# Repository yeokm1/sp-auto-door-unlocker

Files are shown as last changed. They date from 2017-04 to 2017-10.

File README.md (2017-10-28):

# Auto Door Unlocker

A device at the exit that unlocks the main office door of the Singapore Power Digital Team's office at Keppel Tower 2 with just a hand gesture. There are several iterations

1. Passive Infrared (PIR) sensor
2. Active IR sensor
3. Active IR and Ultrasonic sensor

## Demo media

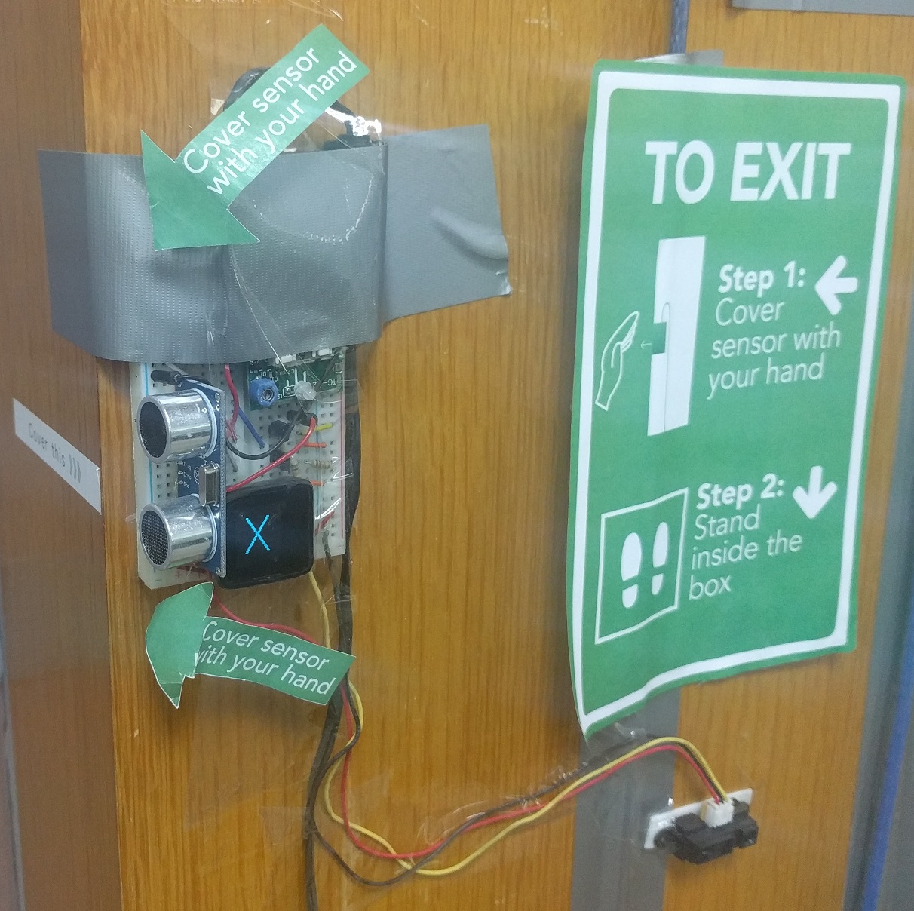
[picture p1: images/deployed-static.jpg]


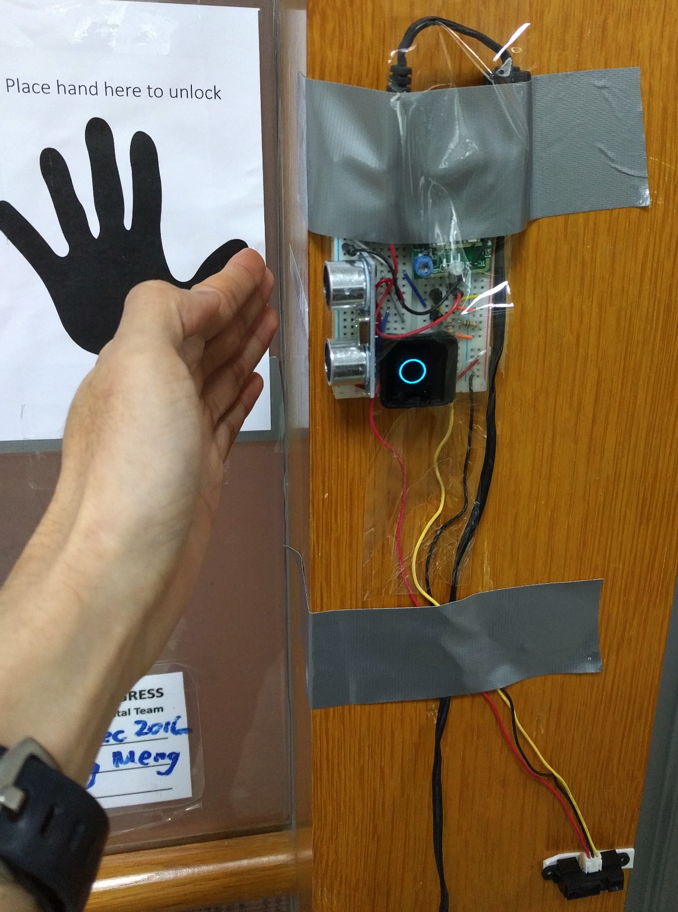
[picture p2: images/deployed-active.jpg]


(https://www.youtube.com/watch?v=IeWPlm1Xaz0)

## How it works?

This device leverages on the original wireless remote to do the unlocking as seen in the picture below.

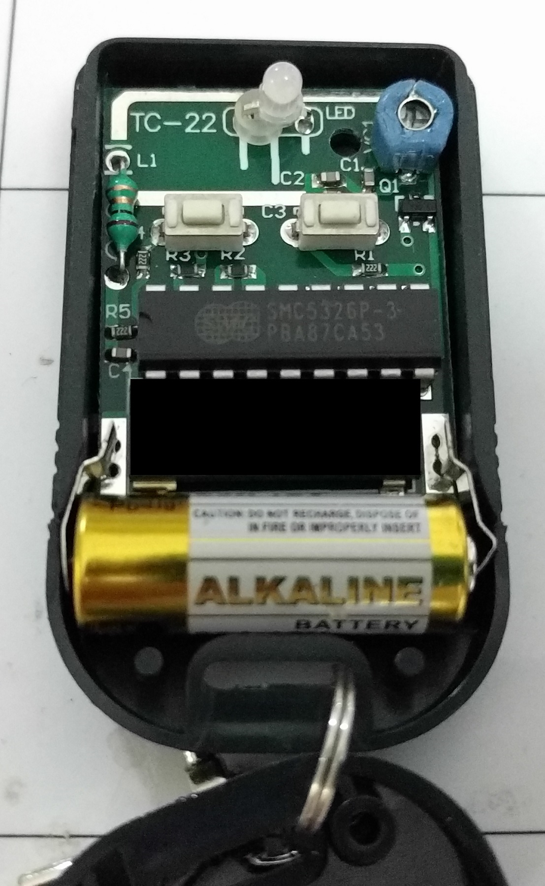
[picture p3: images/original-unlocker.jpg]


To detect the hand gesture, an active Infrared Sensor is used to detect changes in the environment infrared signature.

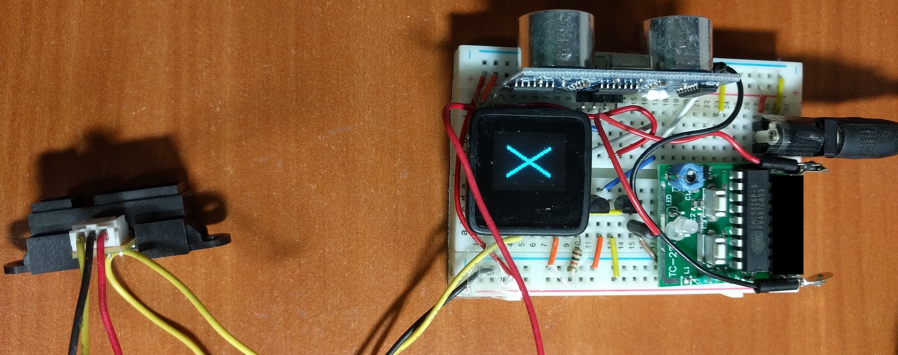
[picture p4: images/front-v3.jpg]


The IR sensor sends an analog signal to the Microview microcontroller indicating the distance of the object in front of it. If the threshold is hit, the Microview then simulates a button press by applying a voltage on the button circuit on the remote to send the wireless signal to unlock the doors. An animation is also shown on the OLED screen of the Microview.

A 2 seconds delay is imposed on the initial power on of the device to let the sensors "settle" down

## Schematic

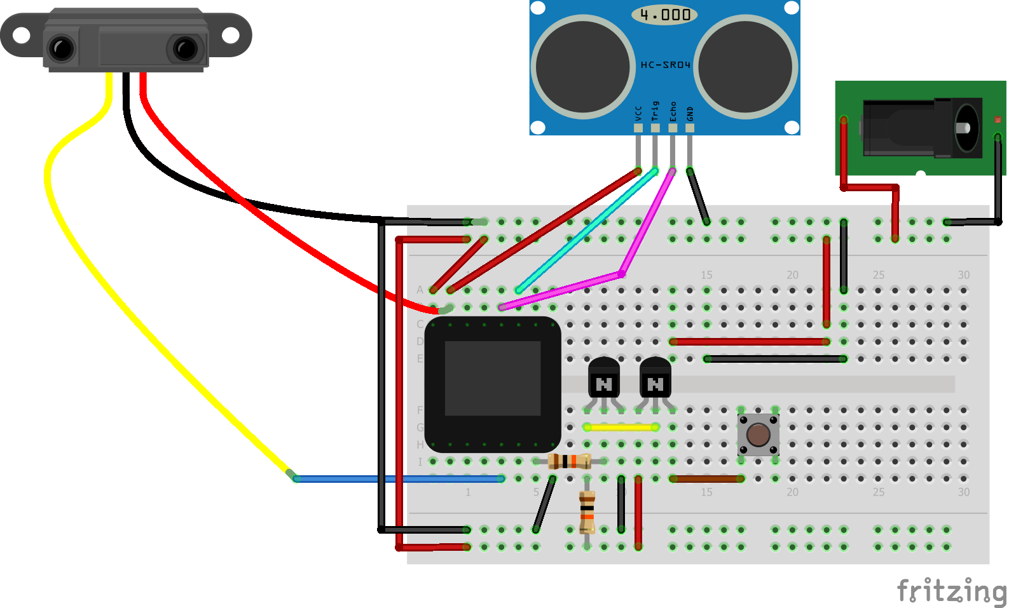
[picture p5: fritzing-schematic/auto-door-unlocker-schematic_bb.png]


A Fritzing drawing indicates the connections on the breadboard. Note this is just a guide of connection and not representative of the actual physical layout.

The button circuit on the remote requires a 12V input to engage. I had to use 2 transistors to switch the input as the output pin on both the Microview do not seem to be able to saturate the transistor. Engaging the button requires an opposite signal, output LOW to "press" the button and vice-versa.

## Parts required
1. MV1: [Microview module](https://www.sparkfun.com/products/12923)
2. J3: [Sharp GP2Y0A21YK IR sensor 10-80cm](http://www.sgbotic.com/index.php?dispatch=products.view&product_id=20)
3. hc-sr1: [HC-SR04 v2](http://www.sgbotic.com/index.php?dispatch=products.view&product_id=1855)
3. R1 and R2: 10K ohm resistors
4. U1 and U2: [P2N2222A NPN transistor](http://www.sgbotic.com/index.php?dispatch=products.view&product_id=773)
5. J2: [2.1mm DC barrel jack](https://www.adafruit.com/product/373)

## Setting up the IDE for compilation

1. Programming the Microview requires one-time use of the [Microview USB Programmer](https://www.sparkfun.com/products/12924)
2. You can follow the Arduino set up guide in this [link](http://microview.io/intro/getting-started.html) which is summarised in the subsequent steps I recommend the native Arduino IDE instead of Codebender.
3. Download the latest [Arduino IDE](https://www.arduino.cc/en/Main/Software) which is version 1.6.13 at time of writing.
4. `git clone https://github.com/geekammo/MicroView-Arduino-Library.git` to your Arduino library folder which is `~/Documents/Arduino/libraries` directory on Macs.
5. Open the `auto-door-unlocker-code` file with the Arduino IDE and select Arduino/Genuino Uno as the board type. Make sure to choose the correct serial port associated with the USB programmer.
6. Just hit upload button to program the board.

## References and libraries

1. [Control 12V from 5V signal](https://electronics.stackexchange.com/a/70246)
2. [Hand image](https://pixabay.com/p-297767/)
3. [Sharp IR library](https://github.com/guillaume-rico/SharpIR)
4. [Ultrasonic HC-SR04](http://randomnerdtutorials.com/complete-guide-for-ultrasonic-sensor-hc-sr04/)

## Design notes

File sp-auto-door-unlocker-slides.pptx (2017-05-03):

## SP Office Gadget: Auto Door Unlocker

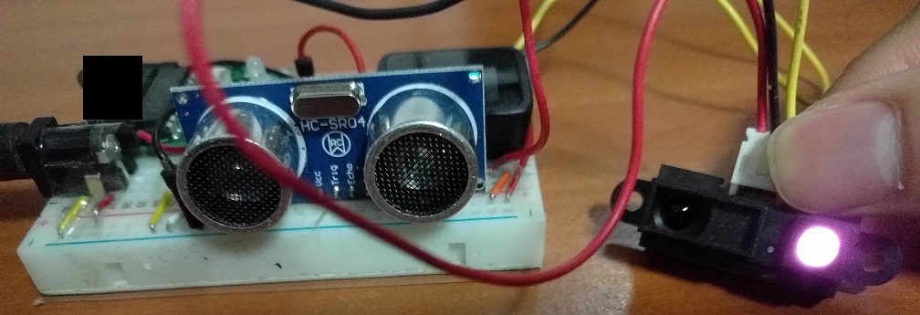
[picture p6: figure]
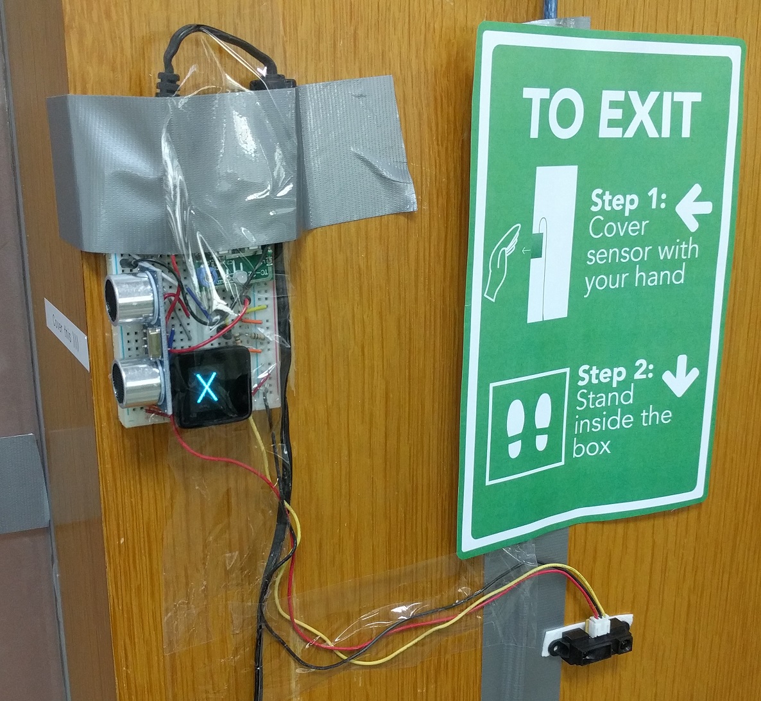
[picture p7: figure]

By: Yeo Kheng Meng (yeokm1@gmail.com)
https://github.com/yeokm1/sp-auto-door-unlocker


Hackware v3.0 (3 May 2017)
SP Digital Tech Talk (29 Dec 2016)

## Problem?

- Tap staff pass on exit
  - Trouble for visitors
  - Hassle of taking out pass
- Solution:
  - Exit without tapping pass

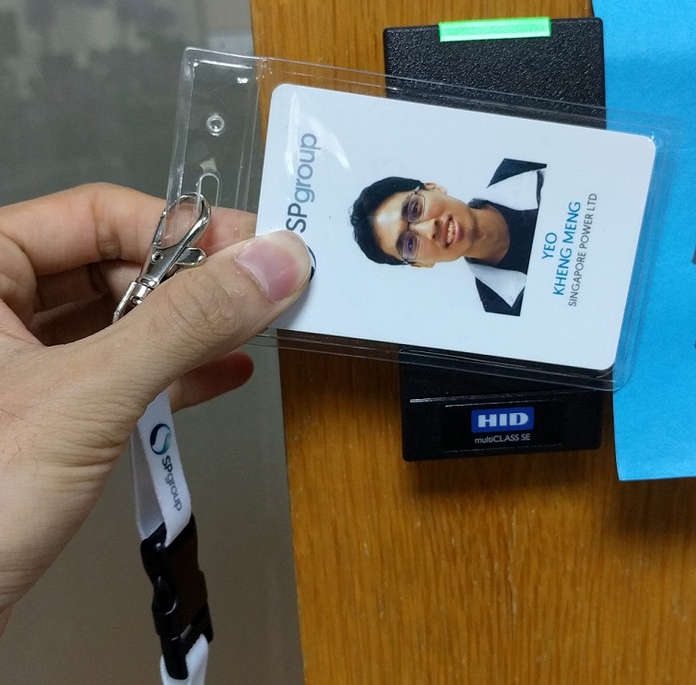
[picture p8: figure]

## Demo Video

https://www.youtube.com/watch?v=IeWPlm1Xaz0

## Wireless remote unlocker

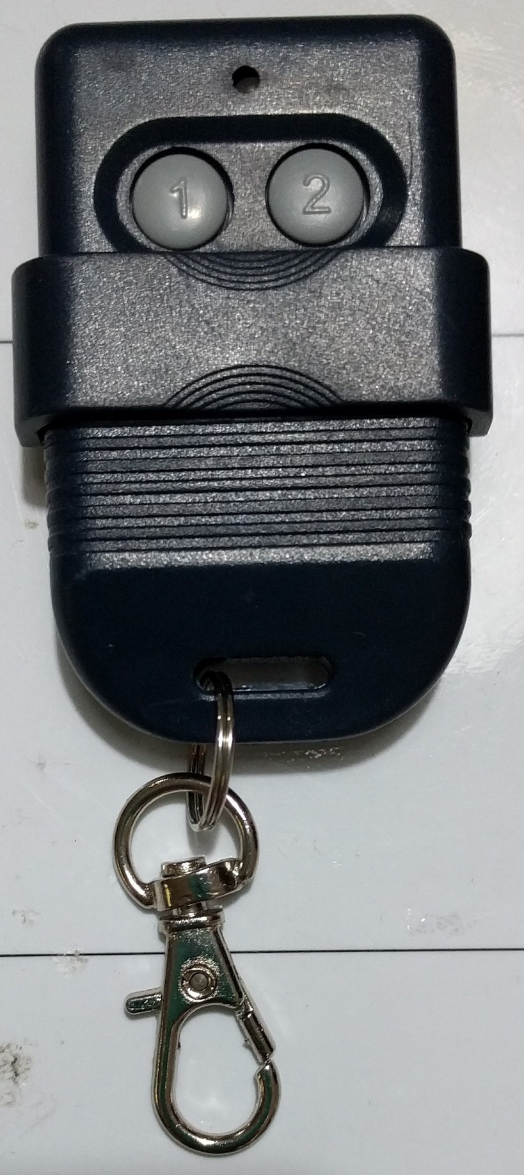
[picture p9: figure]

- 12V battery source
- 2 buttons
- DIP code-select switch
- Voltage-controlled oscillator (VCO)
  - Frequency determined by voltage
- 330Mhz SMC5326P-3
  - Some China chip
  - Unknown function
  - Cannot locate data sheet

## How the button triggers the signal?

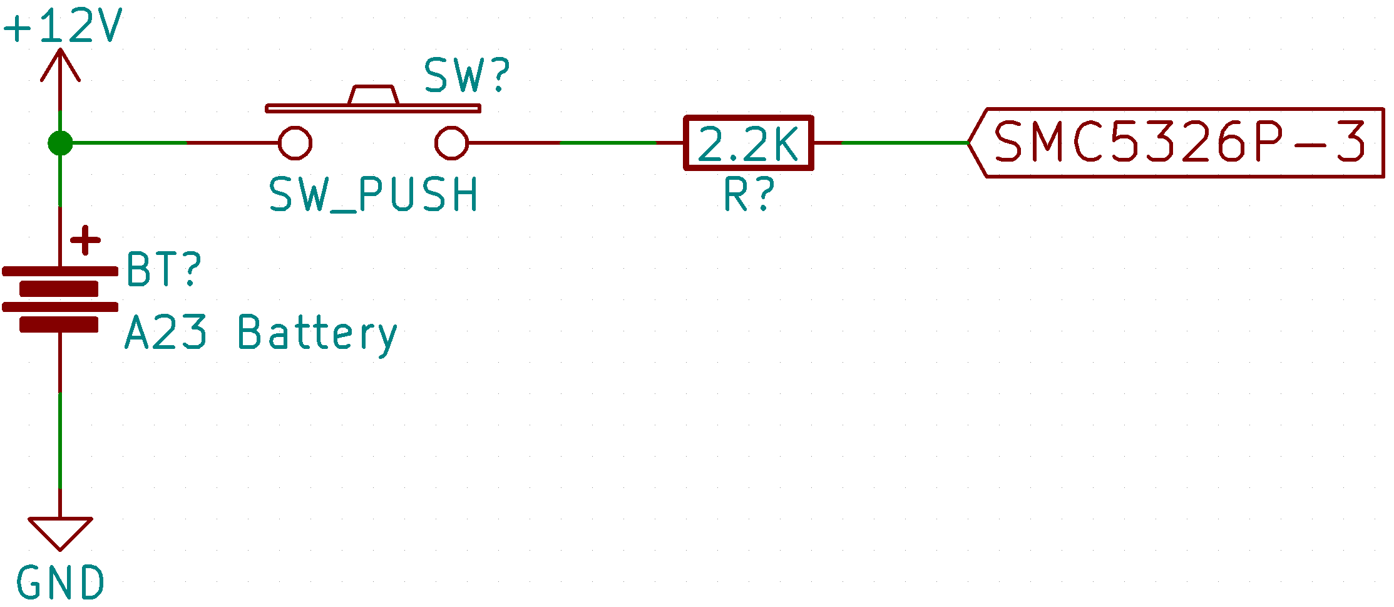
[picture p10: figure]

## An electronic switch: Transistor

- Control current flow with another current flow

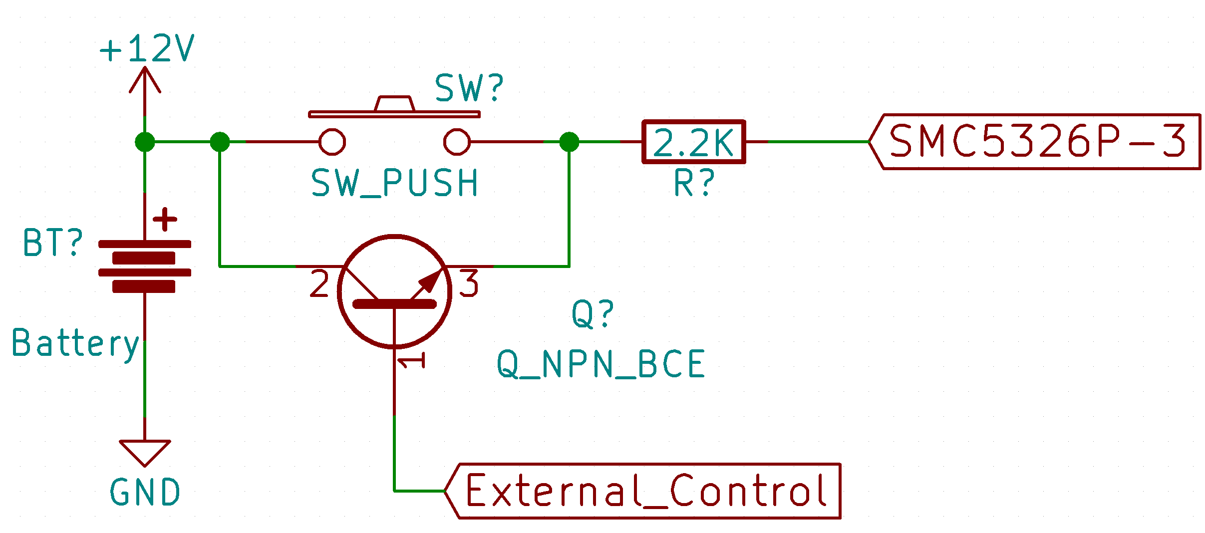
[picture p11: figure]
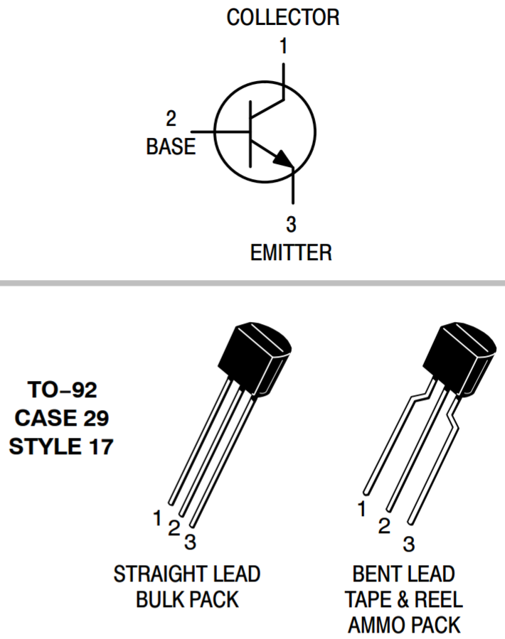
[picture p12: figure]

## The trigger: Active IR + Ultrasonic Sensor

- Ultrasonic HC-SR04 v2
  - 3.3V logic compatible
  - Physical Domain
- Infrared (IR) Distance Sensor GP2Y0A21YKR
  - Effective range: 10 to 80cm
  - Active IR
  - Electromagnetic domain
- => Multi-modal integration / Sensor Fusion to avoid errors

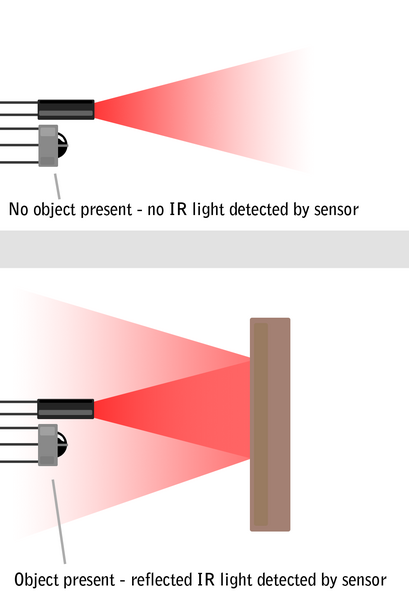
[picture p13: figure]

Source: http://education.rec.ri.cmu.edu/content/electronics/boe/ir_sensor/1.html

## The brain: Microview

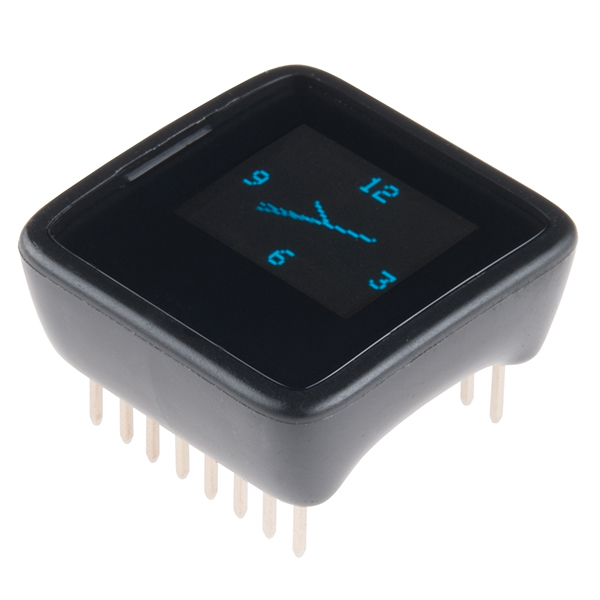
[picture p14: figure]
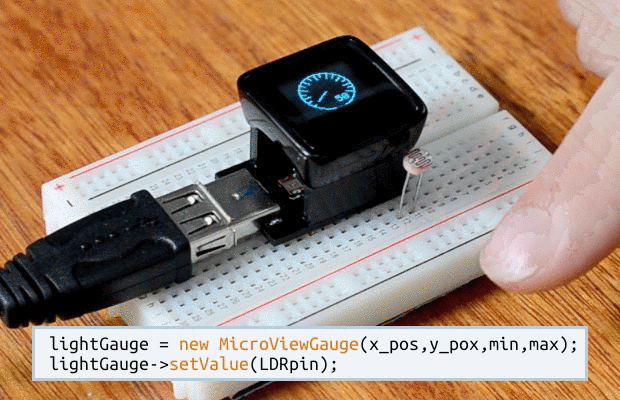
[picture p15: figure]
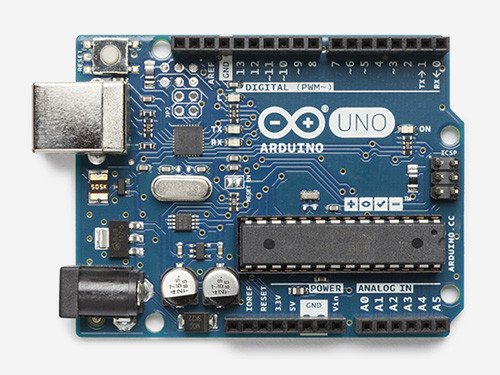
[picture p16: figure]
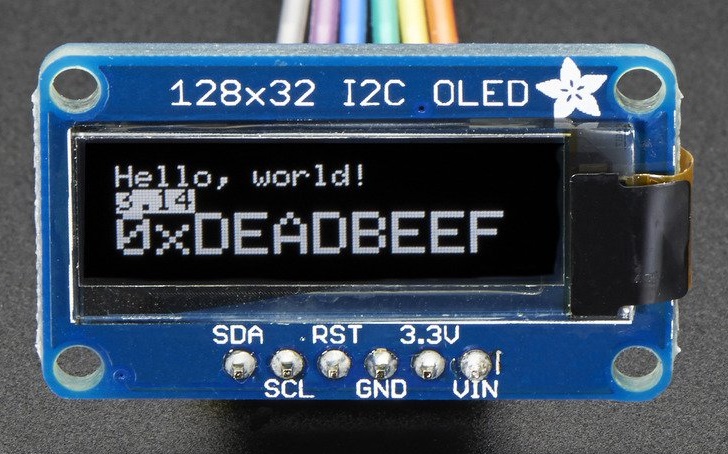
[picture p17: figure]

=

+

- Microview = Arduino + 64x48 OLED screen
- Runs on ATmega328P chip as with Arduino Uno

Source: http://makezine.com/2014/03/25/interview-with-marcus-schappi/

## Wireless Remote Modification

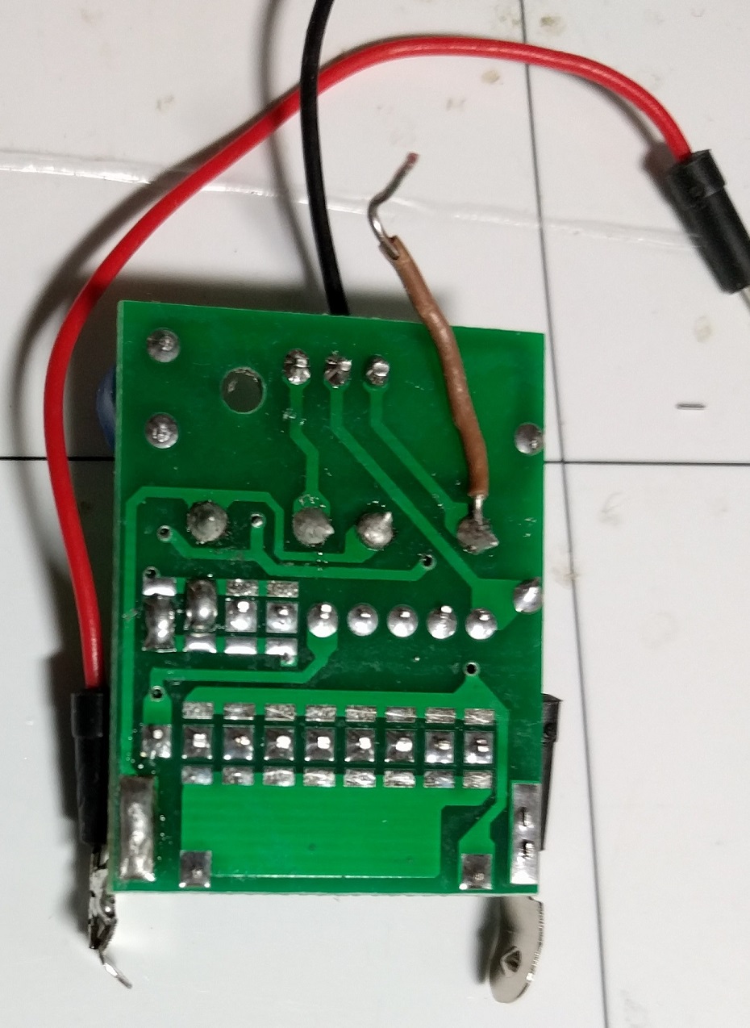
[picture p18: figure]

- Extend button circuit (brown)
- External 12V power (red and black)

## Assembly


- Additional Components
  - Breadboard
  - 12V DC Power Adapter

## Final Product

## Questions?

By: Yeo Kheng Meng (yeokm1@gmail.com)
https://github.com/yeokm1/sp-auto-door-unlocker

## Control 12V signal with 5V

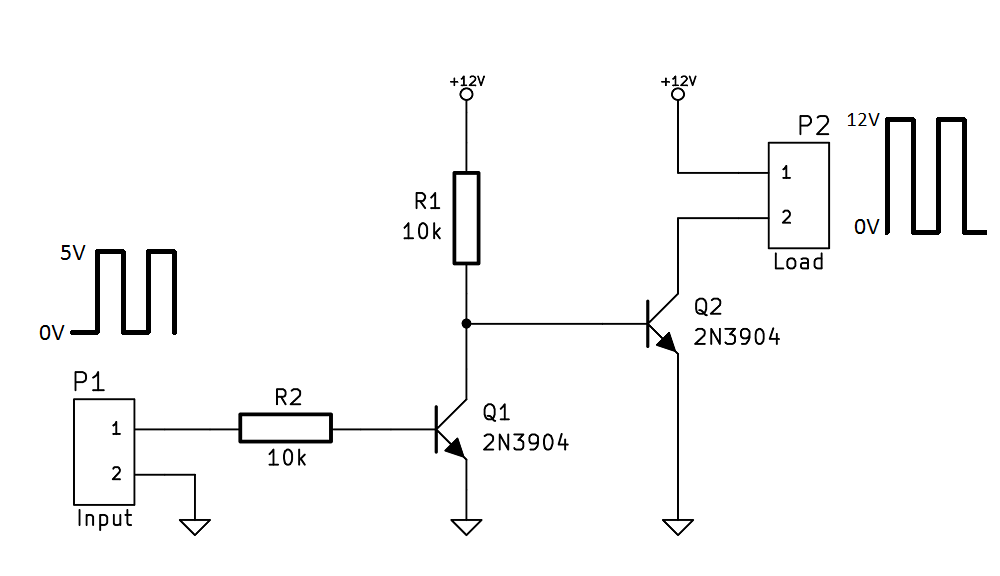
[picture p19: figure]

- Microview 5V Logic Level
- Remote is 12V Logic Level
- -> Active-Low Dual NPN transistor

Source: https://electronics.stackexchange.com/a/70246

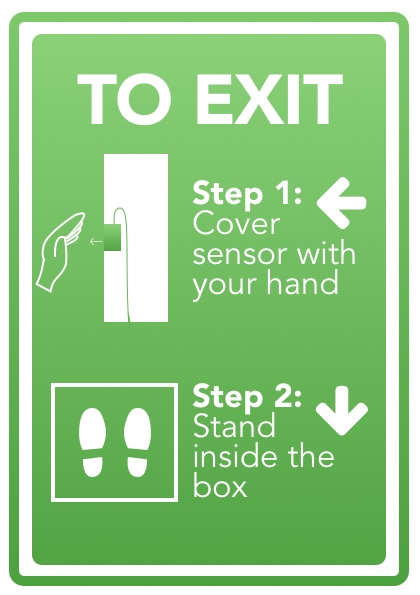
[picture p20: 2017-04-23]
design/Exit Sign.jpg

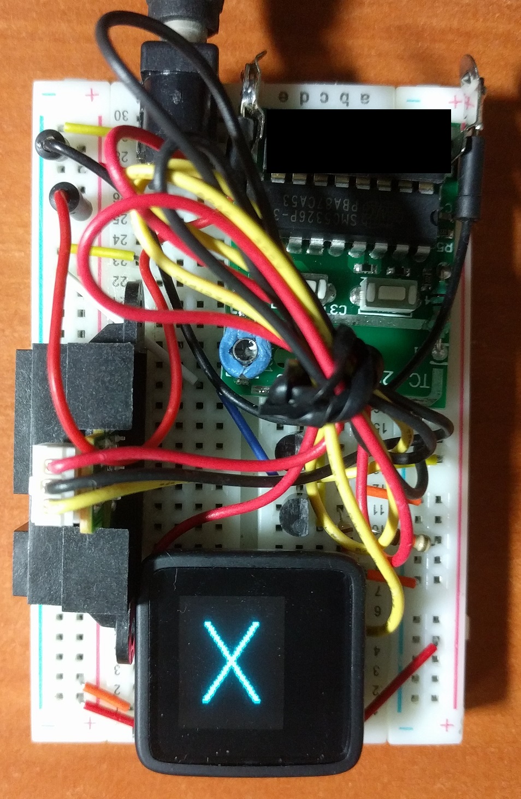
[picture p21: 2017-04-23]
images/front-v2.jpg

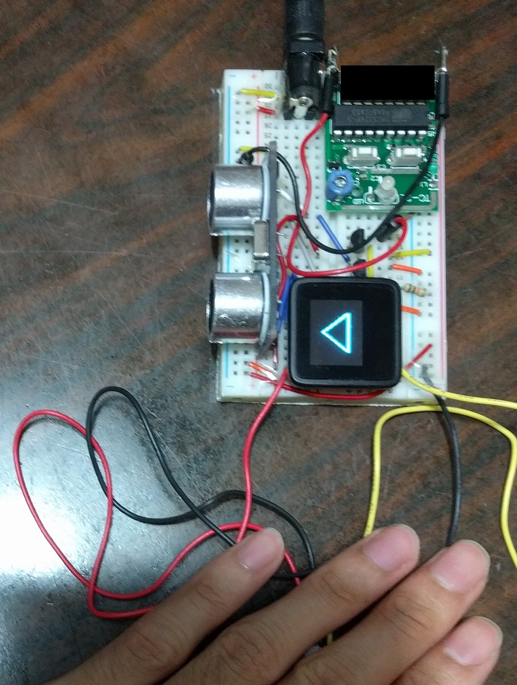
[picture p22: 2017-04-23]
images/cover-ir-sensor.jpg

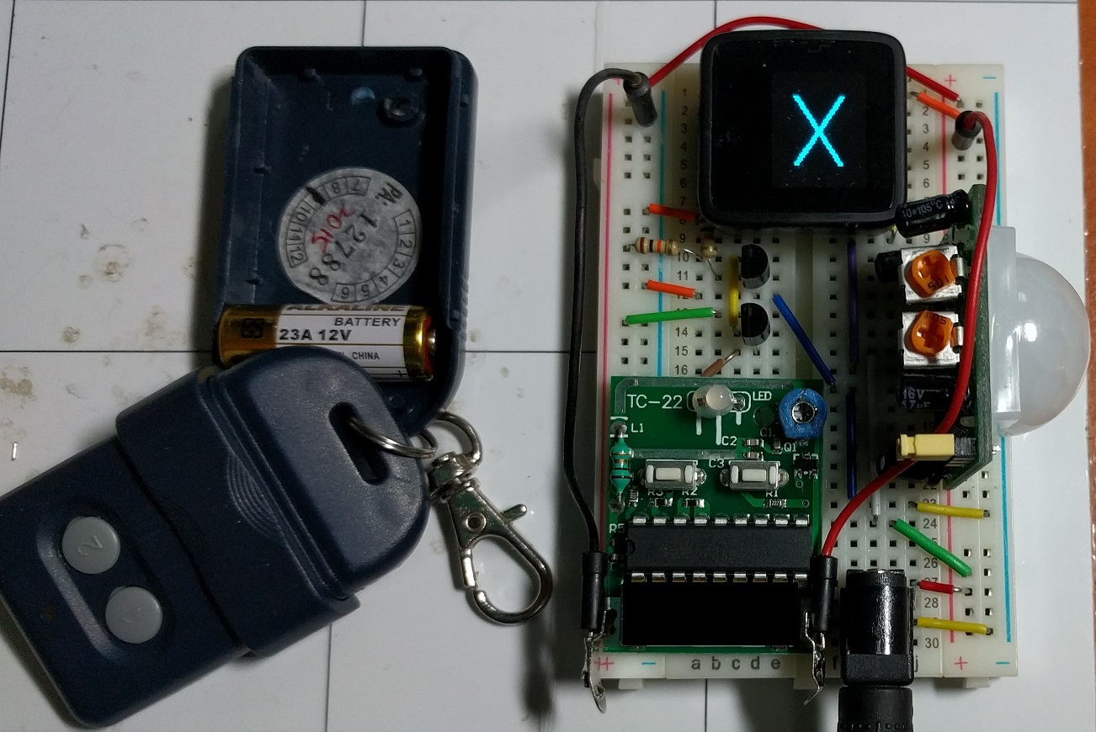
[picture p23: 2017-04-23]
images/front-v1.jpg

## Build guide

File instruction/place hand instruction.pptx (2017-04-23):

## Place hand here to unlock

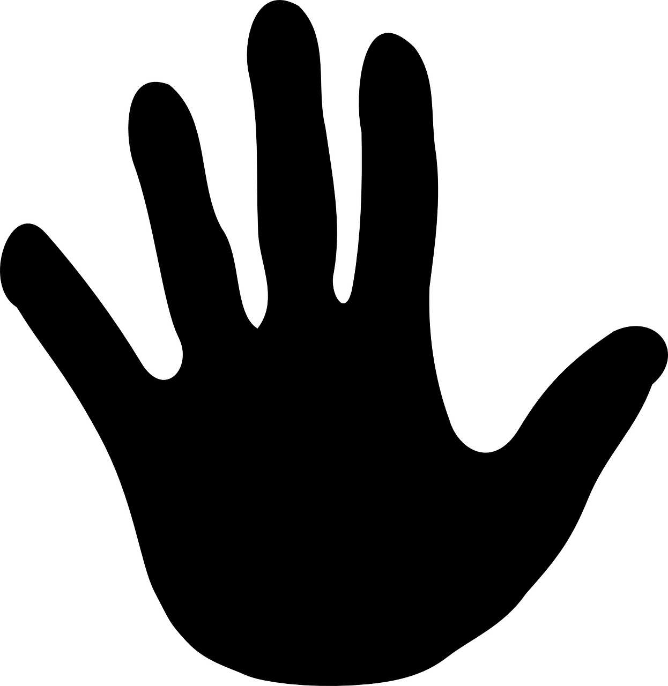
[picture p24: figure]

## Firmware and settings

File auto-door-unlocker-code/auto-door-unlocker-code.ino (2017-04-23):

#include <MicroView.h>
#include "SharpIR.h"

#define DISTANCE_IR_THRESHOLD 60 //cm
#define DISTANCE_US_THRESHOLD 20 //cm

#define TIMES_TO_PASS_BEFORE_ENGAGE 5

#define PIN_IR_SENSOR A2
#define PIN_BUTTON_CONTROL A0

#define PIN_US_TRIG 2
#define PIN_US_ECHO 3

#define MIN_ENGAGE_TIME 200

#define DELAY_BEFORE_START 2 //Wait x seconds for sensor to settle down
#define INTERVAL_ANIM_CHANGE 300

#define model 1080 //1080 for GP2Y0A21Y
SharpIR * sharpIR;

bool currentAnimState = false;
unsigned long previousAnimChangeTime;

bool currentlyEngaged = false;
unsigned long timeLastEngaged;

int timesPassedThreshold = 0;

void setup(){

  pinMode(OUTPUT, PIN_BUTTON_CONTROL);
  //Immediately turn off signal to remote as the default is high
  engageRemote(false);

  Serial.begin(9600);

  pinMode(INPUT, PIN_IR_SENSOR);
  pinMode(PIN_US_TRIG, OUTPUT);
  pinMode(PIN_US_ECHO, INPUT);

  sharpIR = new SharpIR(PIN_IR_SENSOR, model);
  
  uView.begin();    // begin of MicroView
  uView.clear(ALL); // erase hardware memory inside the OLED controller
  uView.clear(PAGE);  // erase the memory buffer, when next uView.display() is called, the OLED will be cleared.

  previousAnimChangeTime = millis();
  timeLastEngaged = millis();

  unsigned long startMillis = millis();

  for(int i = DELAY_BEFORE_START; i > 0; i--){
    uView.clear(PAGE);
    uView.setCursor(0, 0);

    //Large Font for seconds
    uView.setFontType(1);
    uView.print(i);
    uView.println("s");

    //Smaller font for others
    uView.setFontType(0);
    uView.print("for \nsensors tostabilise"); //No space between "to" and "stabilise" as they are on separate lines
    uView.display();
    delay(1000);
  }

  Serial.println("Setup complete");
}


void loop(){


  int usDistance = getUSDistance();
  int irDistance = sharpIR->distance();

//  Serial.print(usDistance);
//  Serial.print(" ");
//  Serial.println(irDistance);

  uView.setCursor(0,0);

  if(irDistance <= DISTANCE_IR_THRESHOLD && usDistance <= DISTANCE_US_THRESHOLD){

    timesPassedThreshold++;

    if(timesPassedThreshold > TIMES_TO_PASS_BEFORE_ENGAGE){
      //To prevent unlimited increment
      timesPassedThreshold = TIMES_TO_PASS_BEFORE_ENGAGE;
      
      currentlyEngaged = true;
      timeLastEngaged = millis();
      engageRemote(true);
      drawChangingCircle();
    }
    

  } else {

    timesPassedThreshold = 0;
    unsigned long currentTime = millis();

    //Continue to engage button for the minimum time
    if((currentTime - timeLastEngaged) < MIN_ENGAGE_TIME){
      engageRemote(true);
      drawChangingCircle();
      
    } else{
    
     engageRemote(false);
     
     if(irDistance <= DISTANCE_IR_THRESHOLD){
      drawBlinkingLeftArrow();
     } else if(usDistance <= DISTANCE_US_THRESHOLD){
      drawBlinkingDownArrow();
     } else {
      engageRemote(false);
      drawStaticX();
     }
   }

  }

  uView.display();
    
}

void drawBlinkingLeftArrow(){

  unsigned long currentMillis = millis();

  if (currentMillis - previousAnimChangeTime >= INTERVAL_ANIM_CHANGE) {
    uView.clear(PAGE);
    
    previousAnimChangeTime = currentMillis;

    if (currentAnimState) {
      currentAnimState = false;
    } else {
      currentAnimState = true;
      
      uView.line(32,9,54,37);
      uView.line(32,10,54,38);
      uView.line(32,11,54,39);

      uView.line(32,9,10,37); 
      uView.line(32,10,10,38);   
      uView.line(32,11,10,39); 

      uView.line(10,37,54,37);
      uView.line(10,38,54,38);
      uView.line(10,39,54,39);


    }
  }
  
}

void drawBlinkingDownArrow(){


  unsigned long currentMillis = millis();

  if (currentMillis - previousAnimChangeTime >= INTERVAL_ANIM_CHANGE) {
    uView.clear(PAGE);
    
    previousAnimChangeTime = currentMillis;

    if (currentAnimState) {
      currentAnimState = false;
    } else {
      currentAnimState = true;

      uView.line(10,23,54,9); 
      uView.line(10,24,54,10); 
      uView.line(10,25,54,11); 

      uView.line(10,23,54,37);  
      uView.line(10,24,54,38);   
      uView.line(10,25,54,39);  

      uView.line(53,10,53,38); 
      uView.line(54,10,54,38); 
      uView.line(55,10,55,38); 

    }
  }


 
  
}

void drawChangingCircle(){

  unsigned long currentMillis = millis();

  if (currentMillis - previousAnimChangeTime >= INTERVAL_ANIM_CHANGE) {
    uView.clear(PAGE);
    
    previousAnimChangeTime = currentMillis;

    if (currentAnimState) {
      currentAnimState = false;
      uView.circle(32,24,20);
      Serial.println("empty circle");
    } else {
      currentAnimState = true;
      uView.circleFill(32, 24, 15);
    }
  }
}

void drawStaticX(){
  uView.clear(PAGE);

  //3 lines for each part of the X to make it thicker
  uView.line(10,9,54,37);
  uView.line(10,10,54,38);
  uView.line(10,11,54,39);

  uView.line(54,9,10,37); 
  uView.line(54,10,10,38);
  uView.line(54,11,10,39);
  
}


void engageRemote(bool newState){

  //State is inverted due to the way the circuitry works
  if(newState){
    digitalWrite(PIN_BUTTON_CONTROL, LOW);
  } else {
    digitalWrite(PIN_BUTTON_CONTROL, HIGH);
  }
}

int getUSDistance(){

  digitalWrite(PIN_US_TRIG, LOW);
  delayMicroseconds(5);
  digitalWrite(PIN_US_TRIG, HIGH);
  delayMicroseconds(10);
  digitalWrite(PIN_US_TRIG, LOW);

  long duration = pulseIn(PIN_US_ECHO, HIGH);
 
  int distCM = (duration/2) / 29.1;

  delay(10);

  return distCM;
}
